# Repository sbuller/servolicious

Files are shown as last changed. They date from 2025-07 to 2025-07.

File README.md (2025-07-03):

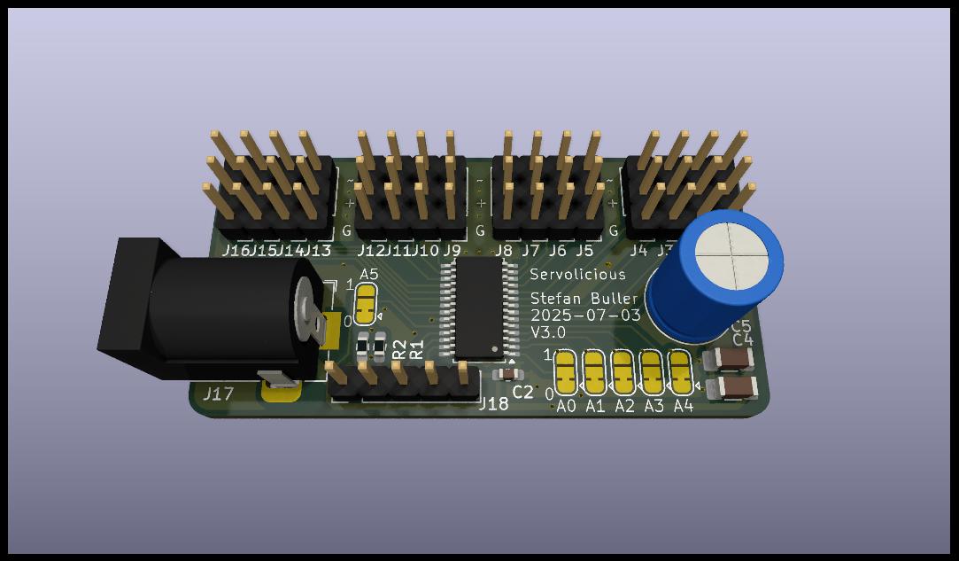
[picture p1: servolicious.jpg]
PCB


A 16 port servo controller. Supply +5V, SDA and SCL.

Servo control is generally pulse widths of 1000-2000us, produced at 50Hz where
one wavelength is 20ms. The PCA9685 does 12bit PWM, counting to 4096. Each
count corresponds to 4.883 us. 1000us is a count of 204.7. A count of 204 should
thus drive a servo fully to one side. 2000us is then 409.4. A count of 410 should
thus drive a servo fully to the other side.

Let x be the position to drive the servo to, between 0 and 1.

y = round( x * (410-204) + 204 )

Now y is the count for which each pulse should be held high.

Phase isn't likely to be important. Set LEDn_ON to 0. Set LEDn_OFF to y.

If necessary, the resolution of the PWM can be improved. By scaling the clock
and adjusting the PWM for each segment, finer control may be managed.

```
Segments: 10
Clock: 500Hz
Segment 1: 2048-4096
Segment 2-10: off
```

```
Segments: 4
Clock: 200Hz
Segment 1: 819-1639
Segments 2-4: off
```

```
Segments: 5
Clock: 250Hz
Segment 1: 1024-2048
Segments 2-5: off
```

```
Segments: 20
Clock: 1000Hz
Segment 1: on
Segment 2: 0-4096
Segments 3-20: off
```

If not controlling /OE and CLK from the uC, pull low. R1 and R2 are
provided for this purpose.

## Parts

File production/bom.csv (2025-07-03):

Designator | Footprint | Quantity | Value | LCSC Part #
C1 | C_Radial_D8.0mm_H11.5mm_P3.50mm | 1 | C_Small_US
C2 | 0603 | 1 | C_Small
C4, C5 | 1206 | 2 | C_Small
J1, J10, J11, J12, J13, J14, J15, J16, J2, J3, J4, J5, J6, J7, J8, J9 | PinHeader_1x03_P2.54mm_Vertical | 16 | Conn_01x03_Pin
J17 | BarrelJack_Horizontal | 1 | Barrel_Jack_MountingPin
J18 | PinHeader_1x05_P2.54mm_Vertical | 1 | Conn_01x05
R1, R2 | 0603 | 2 | R_Small
U2 | TSSOP-28_4.4x9.7mm_P0.65mm | 1 | PCA9685PW

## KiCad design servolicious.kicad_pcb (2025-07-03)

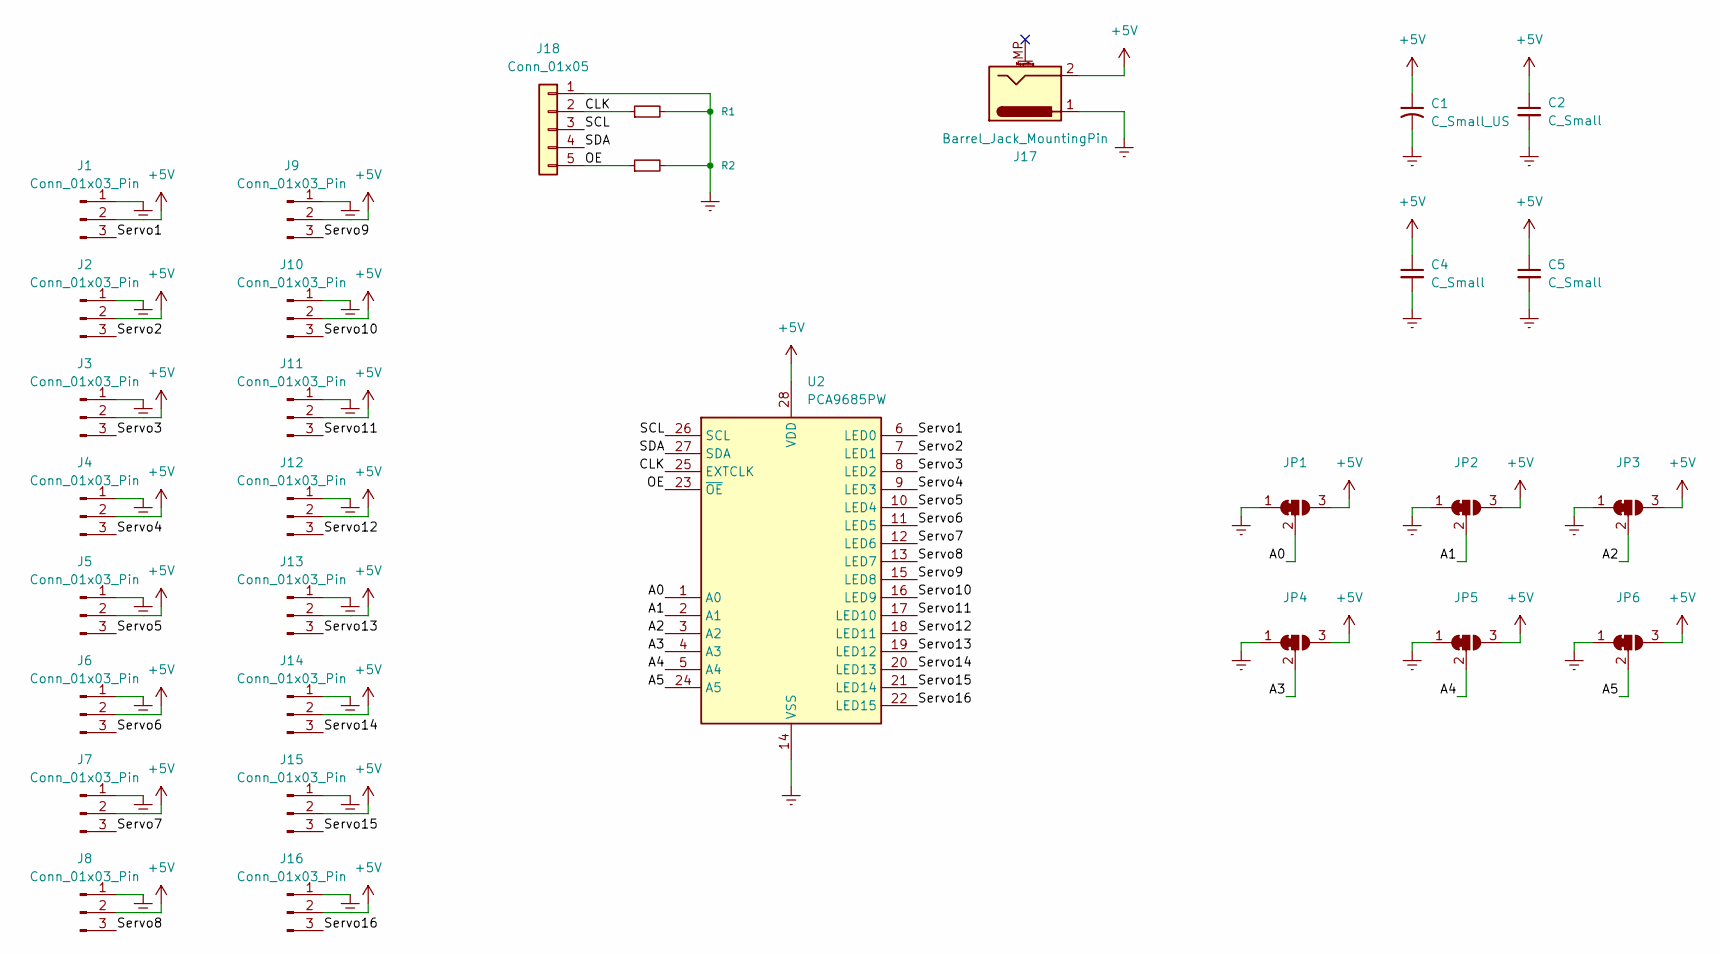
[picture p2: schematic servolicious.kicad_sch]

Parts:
C1: C_Small_US; C_Radial_D8.0mm_H11.5mm_P3.50mm
C2: C_Small; C_0603_1608Metric_Pad1.08x0.95mm_HandSolder
C4, C5: C_Small; C_1206_3216Metric_Pad1.33x1.80mm_HandSolder
J1, J2, J3, J4, J5, J6, J7, J8, J9, J10, J11, J12, J13, J14, J15, J16: Conn_01x03_Pin; PinHeader_1x03_P2.54mm_Vertical
J17: Barrel_Jack_MountingPin; BarrelJack_Horizontal
J18: Conn_01x05; PinHeader_1x05_P2.54mm_Vertical
JP1, JP2, JP3, JP4, JP5, JP6: Jumper:SolderJumper-3_P1.3mm_Bridged12_RoundedPad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; SolderJumper-3_P1.3mm_Bridged12_RoundedPad1.0x1.5mm
R1, R2: R_Small; R_0603_1608Metric_Pad0.98x0.95mm_HandSolder
U2: PCA9685PW; TSSOP-28_4.4x9.7mm_P0.65mm

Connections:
+5V: C1.1, C2.1, C4.1, C5.1, J1.2, J2.2, J3.2, J4.2, J5.2, J6.2, J7.2, J8.2, J9.2, J10.2, J11.2, J12.2, J13.2, J14.2, J15.2, J16.2, J17.2, JP1.3 (B), JP2.3 (B), JP3.3 (B), JP4.3 (B), JP5.3 (B), JP6.3 (B), U2.28 (VDD)
/A0: JP1.2 (C), U2.1 (A0)
/A1: JP2.2 (C), U2.2 (A1)
/A2: JP3.2 (C), U2.3 (A2)
/A3: JP4.2 (C), U2.4 (A3)
/A4: JP5.2 (C), U2.5 (A4)
/A5: JP6.2 (C), U2.24 (A5)
/CLK: J18.2, R1.1, U2.25 (EXTCLK)
/OE: J18.5, R2.1, U2.23 (~OE)
/SCL: J18.3, U2.26 (SCL)
/SDA: J18.4, U2.27 (SDA)
/Servo1: J1.3, U2.6 (LED0)
/Servo2: J2.3, U2.7 (LED1)
/Servo3: J3.3, U2.8 (LED2)
/Servo4: J4.3, U2.9 (LED3)
/Servo5: J5.3, U2.10 (LED4)
/Servo6: J6.3, U2.11 (LED5)
/Servo7: J7.3, U2.12 (LED6)
/Servo8: J8.3, U2.13 (LED7)
/Servo9: J9.3, U2.15 (LED8)
/Servo10: J10.3, U2.16 (LED9)
/Servo11: J11.3, U2.17 (LED10)
/Servo12: J12.3, U2.18 (LED11)
/Servo13: J13.3, U2.19 (LED12)
/Servo14: J14.3, U2.20 (LED13)
/Servo15: J15.3, U2.21 (LED14)
/Servo16: J16.3, U2.22 (LED15)
Earth: C1.2, C2.2, C4.2, C5.2, J1.1, J2.1, J3.1, J4.1, J5.1, J6.1, J7.1, J8.1, J9.1, J10.1, J11.1, J12.1, J13.1, J14.1, J15.1, J16.1, J17.1, J18.1, JP1.1 (A), JP2.1 (A), JP3.1 (A), JP4.1 (A), JP5.1 (A), JP6.1 (A), R1.2, R2.2, U2.14 (VSS)

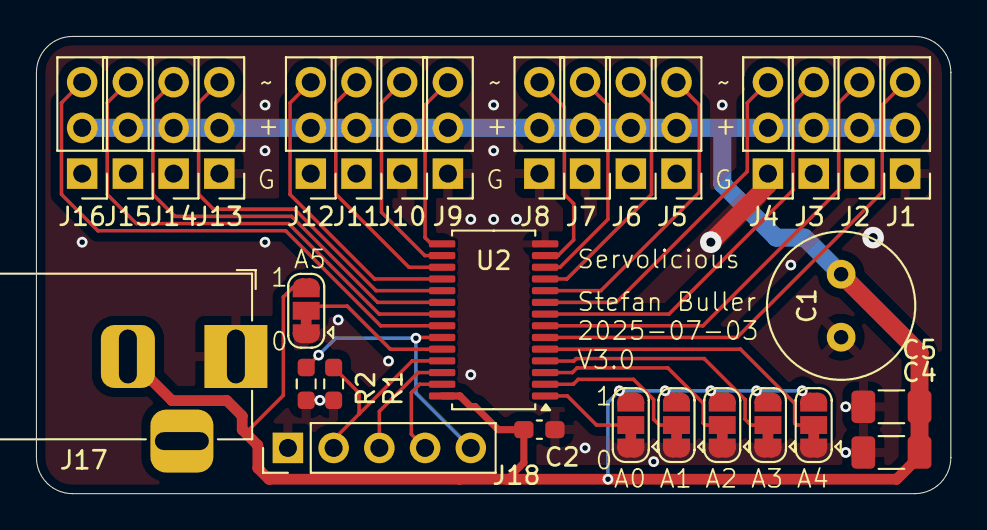
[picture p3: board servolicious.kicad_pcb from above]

Board: 2 copper layers, 50.8 x 25.4 mm, 31 parts (0 on the bottom side), 28 nets.

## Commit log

2025-07-02 Servo headers were wrong
    [servolicious.kicad_pcb, servolicious.kicad_sch]
2025-07-02 Add pretty
    [servolicious.kicad_pcb]
2025-07-02 Switch to latched shift register
    [bom.csv, designators.csv, positions.csv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]
2025-07-02 Add daisy out
    [bom.csv, designators.csv, positions.csv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]
2025-07-02 Add data on servo control to readme
2025-07-03 Use the PCA9685
    [bom.csv, designators.csv, positions.csv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]
2025-07-03 Update README for PCA9685 and rotate cap to allow it to be bent over
    [positions.csv, servolicious.kicad_pcb]
2025-07-03 Interactive PWM control for finer grained management of servos
    [bom.csv, designators.csv, positions.csv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]
